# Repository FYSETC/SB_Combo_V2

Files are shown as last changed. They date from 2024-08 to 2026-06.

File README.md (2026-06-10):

> [!WARNING]
> Do not use the SB1.3 cable directly with V2, their positive and negative poles are in the opposite position.
> We strongly recommend replacing the cable.
> If you do not want to replace the cable, please connect the black of the original 1.3 cable to the + pole and the red to the - pole.

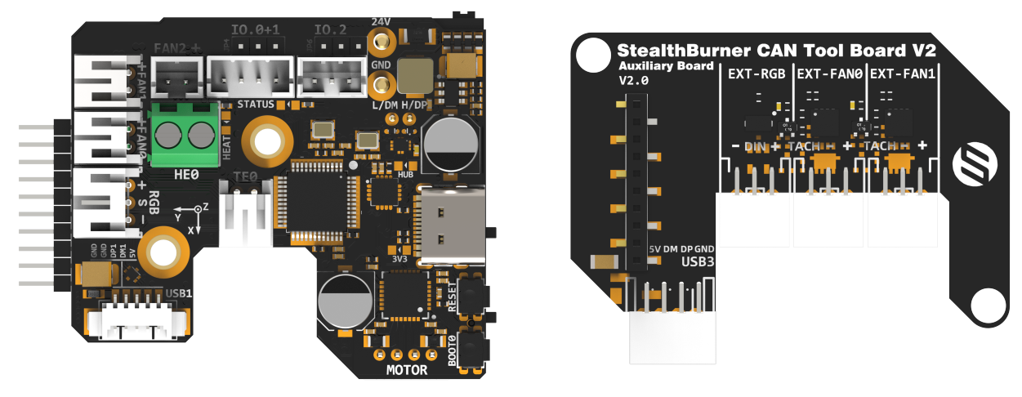
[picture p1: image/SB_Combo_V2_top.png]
SB_Combo_V2_top

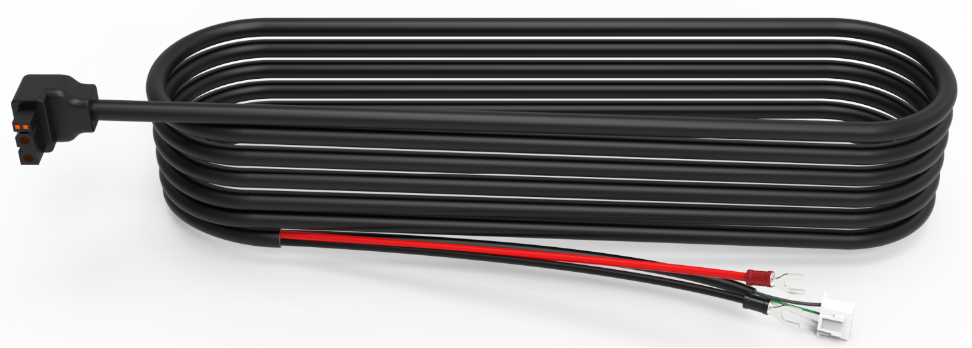
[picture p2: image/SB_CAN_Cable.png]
SB_CAN_Cable


## Introduction:
 SB CAN V2 is a newly designed SB tool board running Klipper firmware. Based on STM32F072, it provides two communication modes: CANBUS and USB. The onboard USBHUB has up to three USB interfaces, which can be used to connect to the scanning leveling sensor (Scanner Leveling Sensor,such as IDM or Cartographer )and AI camera, etc. It can also be connected vertically with an optional board for easy use.

## Features:

- STM32F072 MCU, supports Klipper Firmware

- **6-layer PCB design, all solid capacitors and tantalum capacitors**

- Onboard 2 M3 3.5mm isolation columns, no need for printed parts, easy to install

- Onboard CAN/USB switch

- Onboard RESET and BOOT0 buttons for easy firmware update

- Fan control/heating both use independent high-power MOS, safer and lower heat

- **Onboard 5V@3A DC-DC, 5V peak load can reach 15W**

- XT30 interface, customized connection cable comes with the board

- **Onboard USB2.0 HUB, 3x USB2.0 interface (one of which is located on the auxiliary board)**

- **Support CAN / USB2.0 connection**

- Supports auxiliary board connection For front cover quick install & remove Support 

- Auxiliary board connection for quick installation and removal of the front cover. You can add 1x USB, 2x 3-wire fans, 1x RGB by the auxiliary board

- Onboard TMC2209

- 3x Fans, 3x IO with level converter, 1x RGB,1x Heat, 1x thermistor,1x status LED 

- ADXL345 Accelerometer onboard 

- USB-C onboard for Firmware update

## Documents:

https://wiki.fysetc.com/docs/SBComboV2

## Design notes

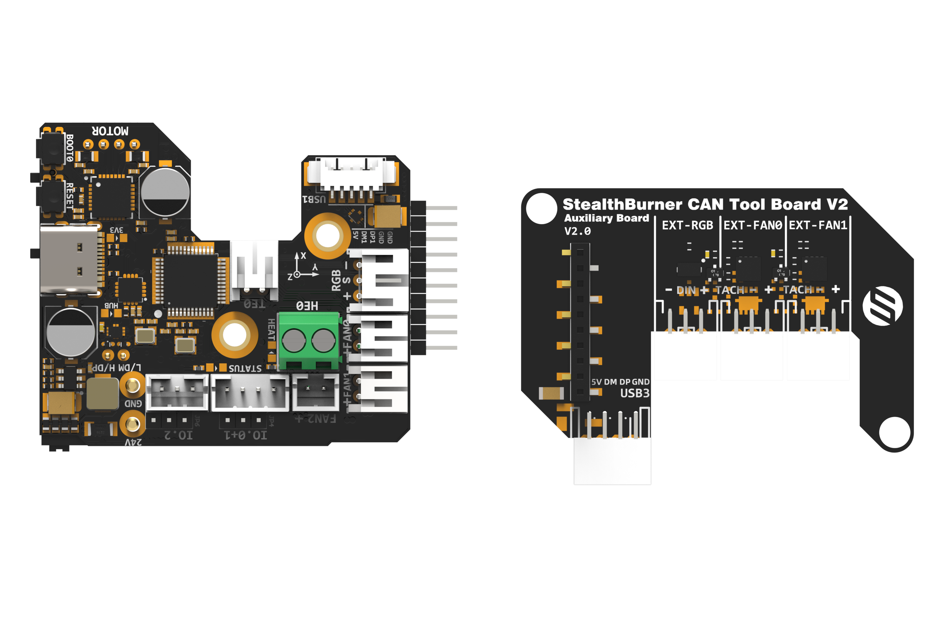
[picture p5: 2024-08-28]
assets/SB_Combo_V2_top.png

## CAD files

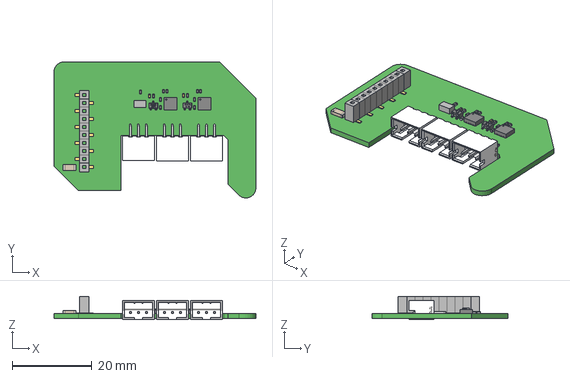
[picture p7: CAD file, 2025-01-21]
3D/SB_CAN_AUX_BOARD V2.step
50.6 x 34.1 x 5.82 mm

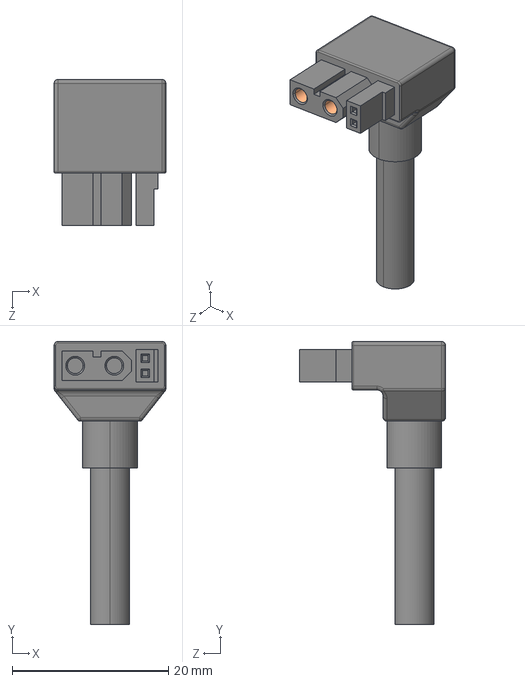
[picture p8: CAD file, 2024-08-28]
3D/XT30_Female.STEP
14.3 x 36.2 x 18.7 mm

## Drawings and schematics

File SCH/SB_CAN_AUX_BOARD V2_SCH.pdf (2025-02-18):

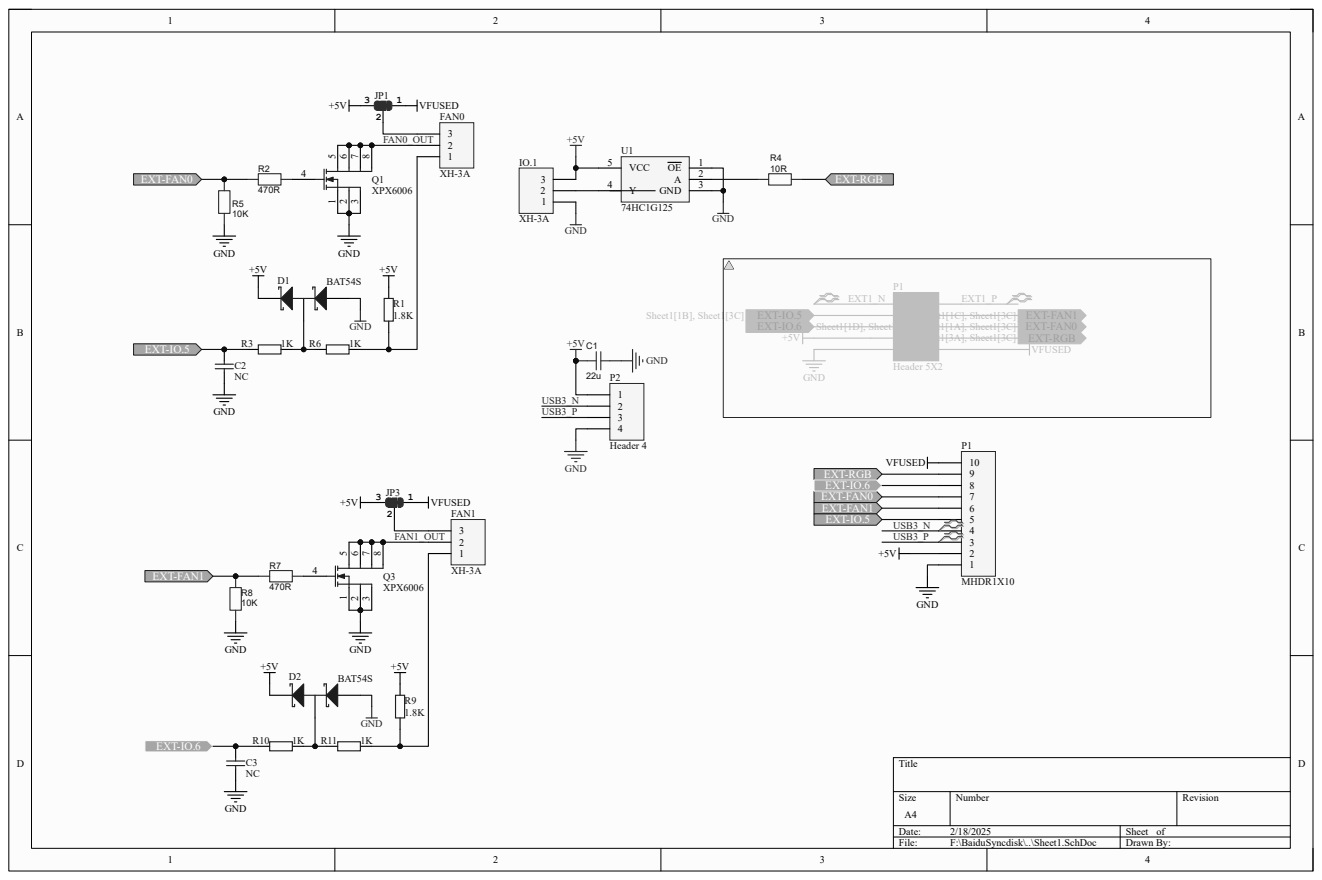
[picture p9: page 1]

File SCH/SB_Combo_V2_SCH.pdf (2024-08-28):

# BRA 23 VS ²⁸

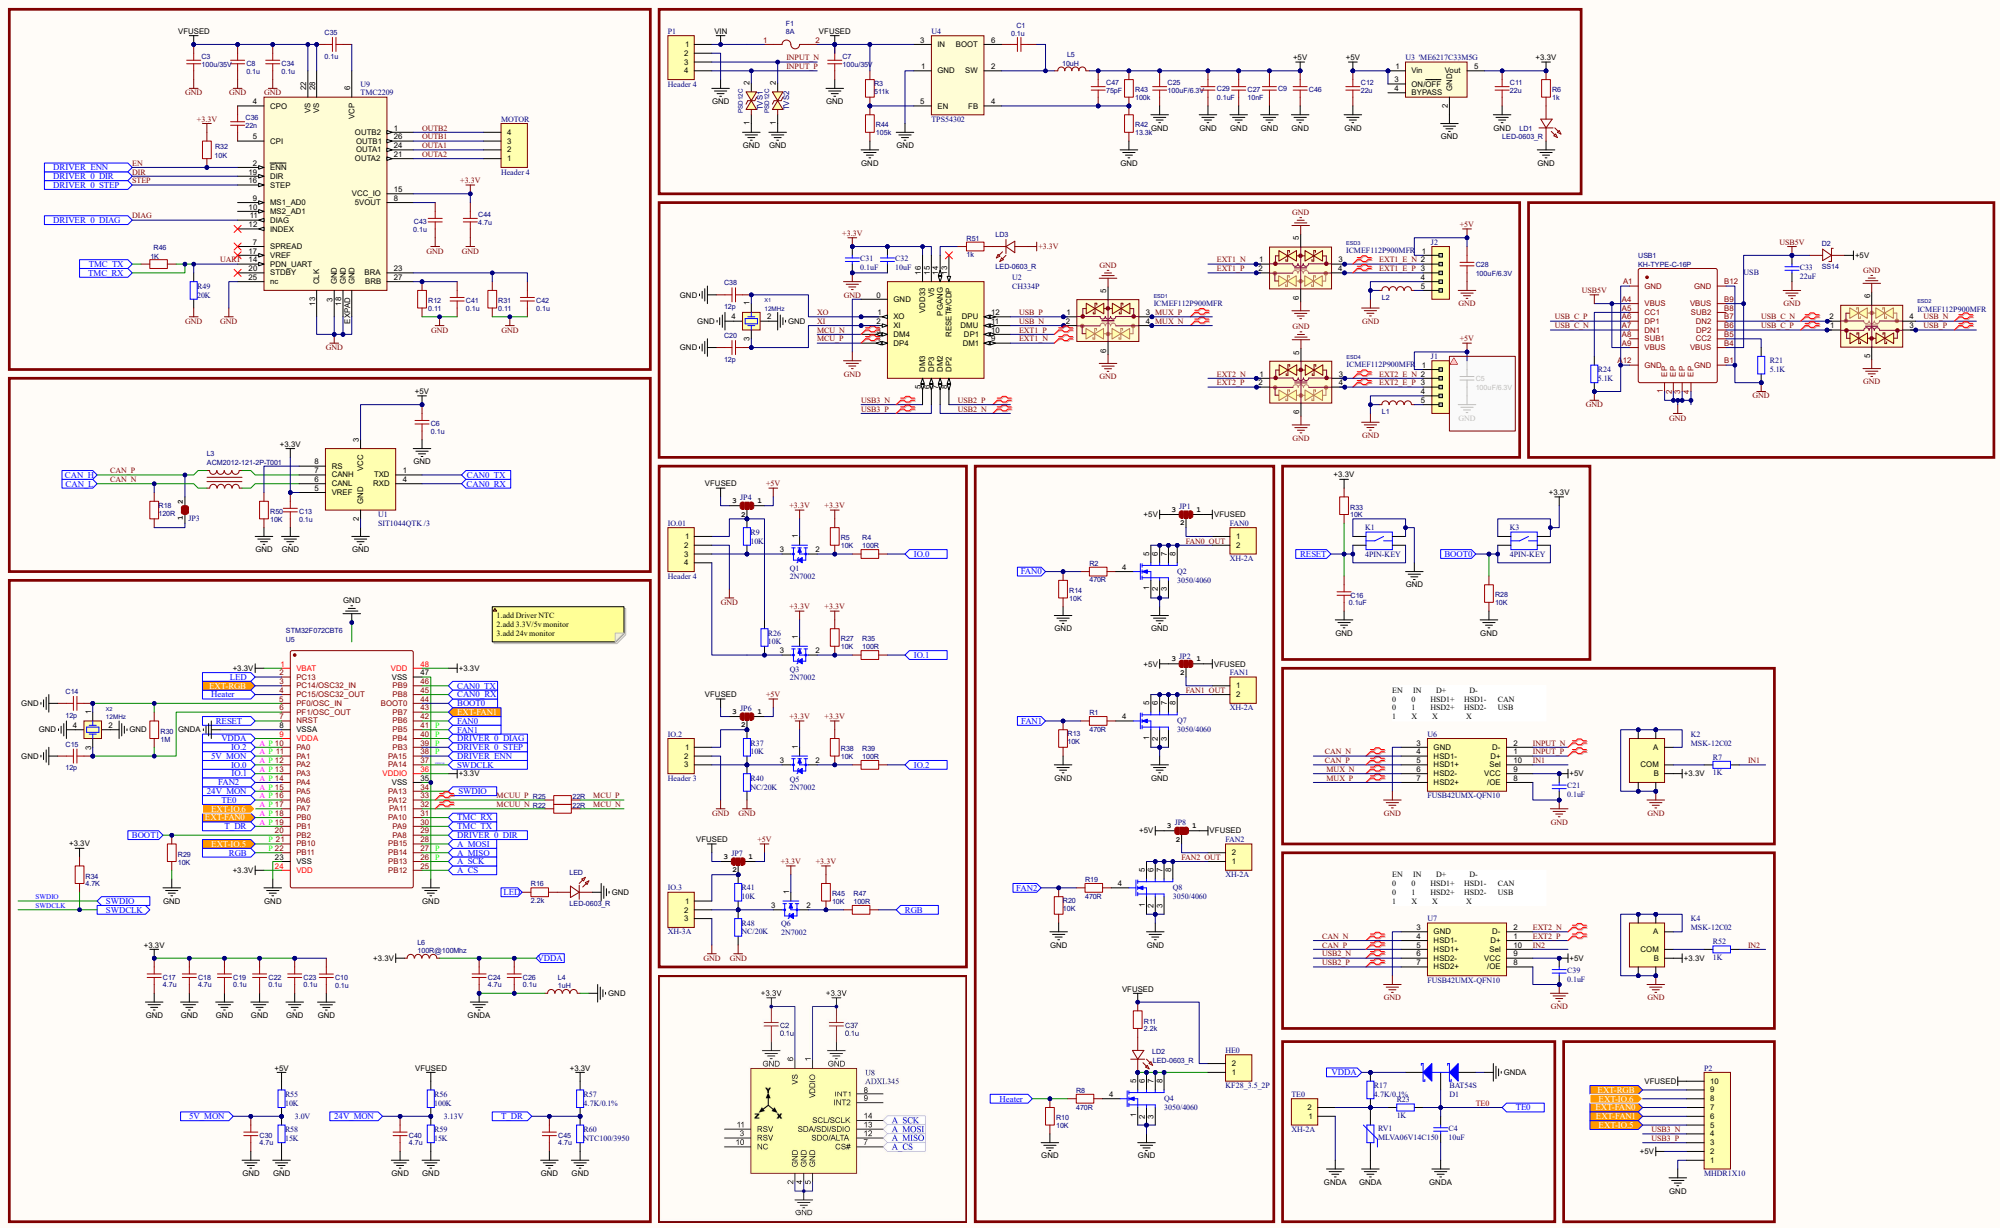
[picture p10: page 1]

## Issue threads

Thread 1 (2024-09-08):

Don't use the SB CAN TH wire on the Fystec 2.4 R2 Pro kit on the V2

darouss99, 2024-09-08:
Hi,

I purchased a Fysetc Voron 2.4 R2 Pro (March 2024 rev). The board that came with it was a SB Can TH, but was DOA. So I had a replacement board. The replacement board is the SB Combo V2. The plug of the wire is right angle so doesn't fit with the March 2024 kit. So I used the original cable that came with the March 2024 kit. Big Error, it's a NO-NO. The +24v and the GND is inverted and there is no reverse polarity protection on the board. Big design flaw for those who will upgrade with this board. The plug should be a standard and the board should have a reverse polarity protection, or at least a big note in the package, github and wiki to not use the cable of the V1 and should have a new bracker for the March 2024 kit or change the right angle plug for a straight one. So now my board is dead again but differently from the first one. This one have clearly a regulator and the TMC chip burned down. Yeah! Magic smoke.

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

darouss99, 2024-10-08:
Hi, I saw that the documentation was changed on the github. It's a great warning for the people. I hope this kind of warning will be added with the board. For now, my board is defective and I'm waiting to know if I need to buy a new board or if I can have a new one under the warranty.  Thank you

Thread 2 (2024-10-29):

no clearance for Gallileo 2

artemen, 2024-10-29:
no clearance for Gallileo 2
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

artemen, 2024-10-29:
and the most prominent:
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

celulari, 2025-02-18:
I've just received my board and now I'm worried about the compatibility with the Galileo 2. @artemen did you install it on the Galileo finally?

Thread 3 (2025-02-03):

Ext_fan0 never spins down fully

jonboy86, 2025-02-03:
I have found my heatbreak fan never spins down fully but will spin up to full power when commended to
just wondering if anyone has seen this

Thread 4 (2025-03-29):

excessive heat on driver

jonboy86, 2025-03-29:
seeing 120 deg C on the driver and motor is also hot

cyberjak2k, 2025-07-11:
2 things to check.
1st check that your run current is reasonable for the purpose and the spec of the motor used,
2nd Make sure that the run current specified in the tmc section for the extruder is actualy telling it to use the one on the sb_combo V2 and not one on the mainboard otherwise it might be defauting to a default vref which will likely be WAY too high for a nema14 36mm

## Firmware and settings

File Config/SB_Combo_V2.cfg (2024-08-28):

[mcu sb_can_th]
serial: /dev/serial/by-id/usb-Klipper_stm32f072xb_1A003B001757474230343220-if00
# canbus_uuid: 314cf360bf26

[extruder]
step_pin: sb_can_th:PB3 #PA7
dir_pin: sb_can_th:PA8 #PA5
enable_pin: !sb_can_th:PA15 #PB4 

##  Update value below when you perform extruder calibration
##  If you ask for 100mm of filament, but in reality it is 98mm:
##  rotation_distance = <previous_rotation_distance> * <actual_extrude_distance> / 100
##  22.6789511 is a good starting point for Bondtech 5mm gears
##  34.37086 for Bondtech 8mm gears (Galileo)
rotation_distance: 4.45   #22.6789511   #Bondtech 5mm Drive Gears
##  Update Gear Ratio depending on your Extruder Type
##  Use 50:17 for Afterburner/Clockwork (BMG Gear Ratio)
##  Use 80:20 for M4, M3.1
##  Use 7.5:1 for Galileo
##  gear_ratio: 50:10               #for Stealthburner/Clockwork2 BMG Gear Ratio
microsteps: 16
full_steps_per_rotation: 200    #200 for 1.8 degree, 400 for 0.9 degree
nozzle_diameter: 0.400
filament_diameter: 1.75
heater_pin: sb_can_th:PC15 #PA8 # Heat
## Check what thermistor type you have. See https://www.klipper3d.org/Config_Reference.html#common-thermistors for common thermistor types.
## Use "Generic 3950" for NTC 100k 3950 thermistors
sensor_type: Generic 3950
sensor_pin: sb_can_th:PA6 #PA0 # TH
min_temp: -273.15 #1 #-273.15 # 1 #zzcatvs mod
max_temp: 99999 #360 #99999 # 360 #zzcatvs mod
max_power: 1.0
min_extrude_temp: 10
#control = pid
#pid_kp = 26.213
#pid_ki = 1.304
#pid_kd = 131.721
##  Try to keep pressure_advance below 1.0
#pressure_advance: 0.02 #0.05
##  Default is 0.040, leave stock
#pressure_advance_smooth_time: 0.040
max_extrude_cross_section: 5000.0

[tmc2209 extruder]
uart_pin: sb_can_th:PA10
tx_pin: sb_can_th:PA9
interpolate: false
run_current: 0.7
sense_resistor: 0.110
stealthchop_threshold: 0
##diag_pin: sb_can_th:PB5

[adxl345]
cs_pin: sb_can_th:PB12
spi_software_sclk_pin: sb_can_th:PB13
spi_software_mosi_pin: sb_can_th:PB15
spi_software_miso_pin: sb_can_th:PB14
axes_map: -y,z,-x

[resonance_tester]
accel_chip: adxl345
probe_points:
    300,300,30 # an example
	
[neopixel sb_leds]
pin: sb_can_th: PB11 #RGB
chain_count: 1
color_order: GRB
initial_RED: 0.5 #0.5
initial_GREEN: 0.5
initial_BLUE: 0.5 #0.5
initial_WHITE: 0.5 #0.5

[neopixel ext_leds]
pin: sb_can_th: PC14 #on the AUX board RGB
chain_count: 1
color_order: GRB
initial_RED: 0.5 #0.5
initial_GREEN: 0.5
initial_BLUE: 0.5 #0.5
initial_WHITE: 0.5 #0.5

#####################################################################
# FANS
#####################################################################

[fan_generic fan0]
pin: sb_can_th:PB6
max_power:1.0
shutdown_speed:0.0
cycle_time:0.5
hardware_pwm:false
kick_start_time:0.10
off_below:0.1

[fan_generic fan1]
pin: sb_can_th:PB5
max_power:1.0
shutdown_speed:0.0
cycle_time:0.5
hardware_pwm:false
kick_start_time:0.10
off_below:0.1

[fan_generic fan2]
pin: sb_can_th:PA4
max_power:1.0
shutdown_speed:0.0
cycle_time:0.5
hardware_pwm:false
kick_start_time:0.10
off_below:0.1

[fan_generic ext_fan0]  # on the AUX board
pin: sb_can_th:PB0
max_power:1.0
shutdown_speed:0.0
cycle_time:0.5
hardware_pwm:false
kick_start_time:0.10
off_below:0.1
tachometer_pin: sb_can_th:PB10
#tachometer_ppr:
#tachometer_poll_interval:

[fan_generic ext_fan1]  # on the AUX board
pin: sb_can_th:PB7
max_power:1.0
shutdown_speed:0.0
cycle_time:0.5
hardware_pwm:false
kick_start_time:0.10
off_below:0.1
tachometer_pin: head:PA7
#tachometer_ppr:
#tachometer_poll_interval:

#####################################################################
#	Mcu & Driver Temperature
#####################################################################

[temperature_sensor can_mcu_temp]
sensor_type: temperature_mcu
sensor_mcu: sb_can_th
min_temp: 0
max_temp: 150

[temperature_sensor Driver_Temp]  # Beside the TMC2209 Chip
sensor_type: Generic 3950
sensor_pin: sb_can_th: PB1
min_temp:0
max_temp:150

#####################################################################
#	Voltage Monitor
#####################################################################

[adc_temperature 5V_Monitor]
temperature1: 5
voltage1: 3.0
temperature2: 4
voltage2: 2.4
temperature3: 3
voltage3: 1.8

[adc_temperature 24V_Monitor]
temperature1: 24
voltage1: 3.13
temperature2: 22
voltage2: 2.87
temperature3: 21
voltage3: 2.74

[temperature_sensor 5V_Monitor]
sensor_type: 5V_Monitor
sensor_pin: sb_can_th:PA1   #5V_MON
adc_voltage: 3.3
voltage_offset: 0

[temperature_sensor 24V_Monitor]
sensor_type: 24V_Monitor
sensor_pin: sb_can_th:PA5   #24V_MON
adc_voltage: 3.3
voltage_offset: 0


#####################################################################
#	PIN Define
#####################################################################

# On the AUX Board

# ext_IO.6: PA7
# ext_fan0: PB0
# ext_IO.5: PB10
# ext_fan1: PB7
# RGB: PC14

# On the SB_Combo Board

# IO.0 and IO.1 are located in the same connector and can be used as XY endstops, 
# and IO.2 can be used as a probe. In addition, IO.0, IO.1, and IO.2 have level 
# conversion (with pull-up resistors) and voltage selectors (5V or 24V), which can 
# be compatible with a variety of sensors. The three IOs and RGB can be used as inputs 
# or outputs, and can be configured according to your needs.

# IO.0: PA2
# IO.1: PA3   
# IO.2: PA0
# RGB: PB11

# FAN0: PB6
# FAN1: PB5
# FAN2: PA4

# Heat: PC15
# Thermistor: PA6

# Driver_EN: PA15
# Driver_DIR: PA8
# Driver_STEP: PB3
# Driver_UART: PA10
# Driver_TX: PA9
# Driver_DIAG: PB4

# spi_bus: spi2
# adxl345_cs_pin: PB12
# adxl345_spi_software_sclk_pin: PB13
# adxl345_spi_software_mosi_pin: PB15
# adxl345_spi_software_miso_pin: PB14

# CAN_RX: PB8
# CAN_TX: PB9

# 5V_Monitor: PA1
# 24V_MOnitor: PA5
# TMC_Thermistor: PB1
